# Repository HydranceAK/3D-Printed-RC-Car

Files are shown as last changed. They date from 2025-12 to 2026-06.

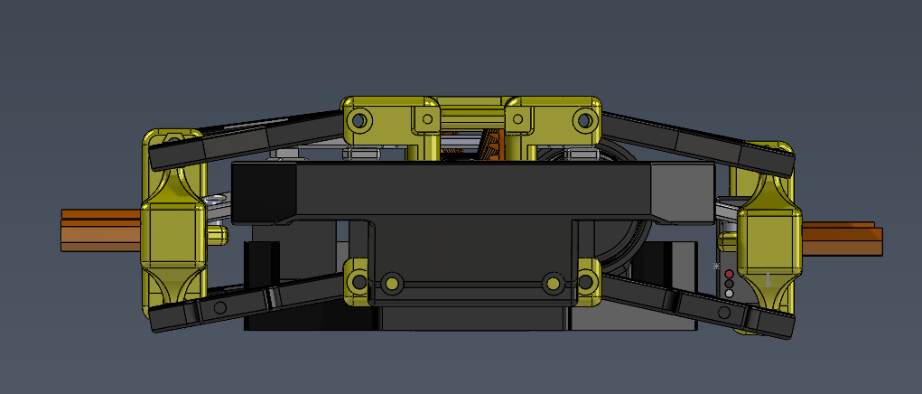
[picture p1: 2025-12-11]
Images & Videos/Screenshot 2025-12-07 164544.png

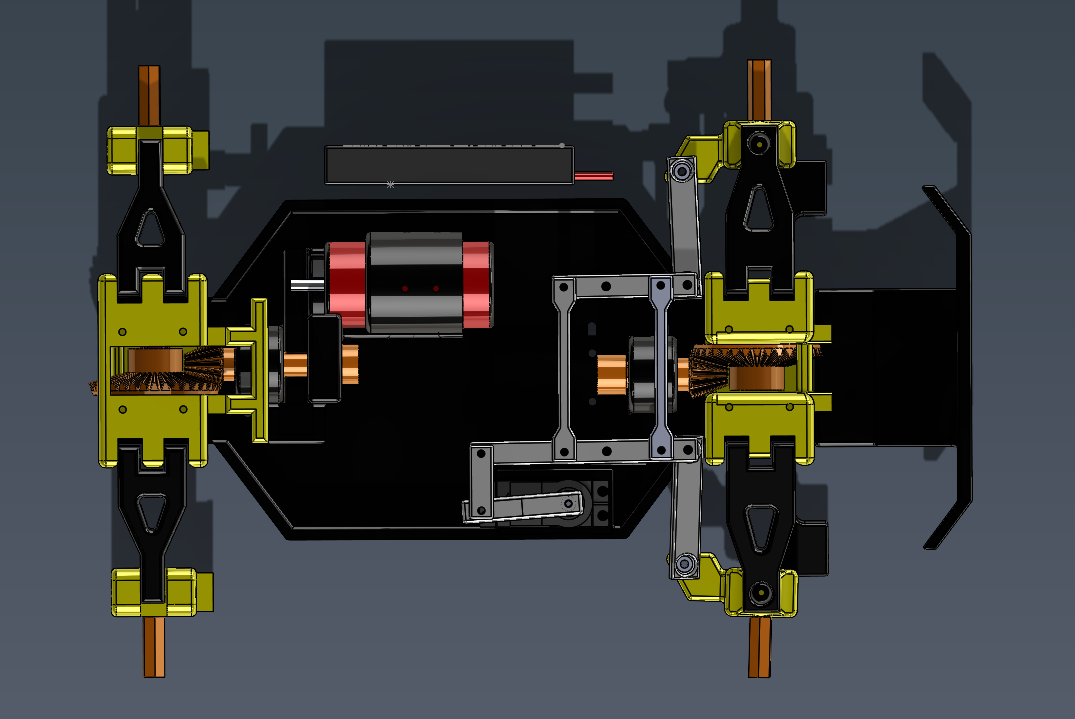
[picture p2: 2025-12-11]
Images & Videos/Screenshot 2025-12-07 164536.png

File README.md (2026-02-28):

**3D Printed RC Car**

A high-performance, fully custom 3D-printed RC car.

video: https://youtu.be/6iFeAaE8pu4

Designed and engineered by ***Hydrance***.

**Features**

* 4WD Drivetrain – Enhanced traction and stability.

* Top Speed: ~60 km/h – High-speed performance

* 90% 3D-Printed Build

* Independent Suspension 

* Durable Materials

* TPU parts for flexible components (tires, dampening mounts, impact zones)

* PETG parts for strong structural elements (chassis, arms, mounts)

* PA6-CF highly recommended but not nessecary for gears and bottom suspension arms. These peices undergo extreme stress and may break if you drive rough.  

* Affordable Build – Total estimated cost ~$330 (without screws \& filament $270)

**Materials \& Printing Notes**

TPU recommended for flexible and shock-absorption components

PETG recommended for strength, heat resistance, and rigidity

Everything can be printed on Bambu Lab a1 (0.4 or 0.6 nozzle)

Hardware, electronics, and drivetrain components sourced Amazon and AliExpress

**Disclaimer**

This project is provided for personal use only.

You may not sell, redistribute, upload, or copy this design without direct permission from the creator.

I am not responsible for any damage, injury, or misuse involving this design, its assembly, or its operation.

Operate RC vehicles safely and responsibly.

**Contact**

For permissions, questions, or collaboration, contact me at:

Email: abdusamaku@gmail.com

YouTube: https://youtube.com/@HydranceYT







WhatsApp Image 2026-01-09 at 2 21 19 PM

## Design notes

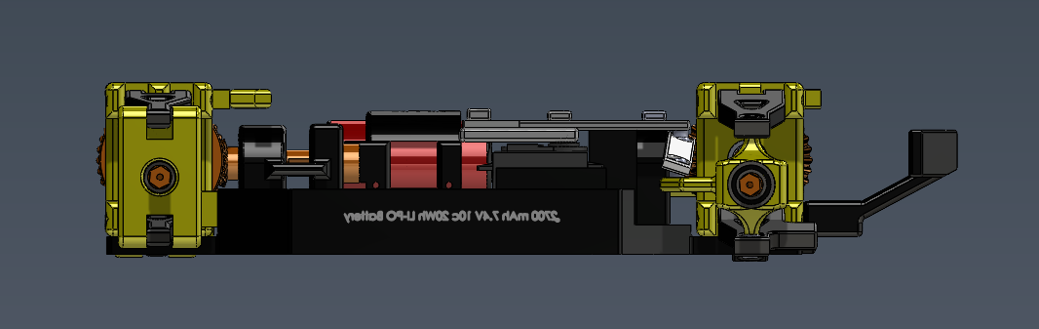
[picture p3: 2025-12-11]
Images & Videos/Screenshot 2025-12-07 164532.png

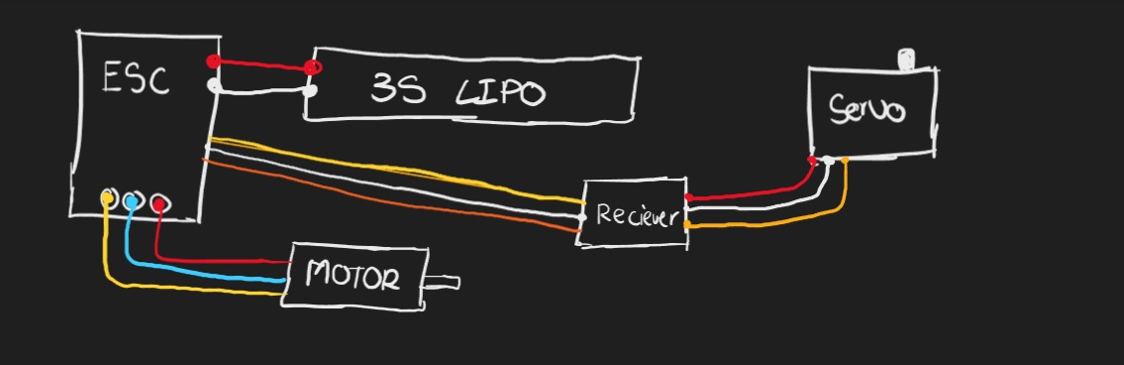
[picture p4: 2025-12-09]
Images & Videos/Circuit Diagram.png

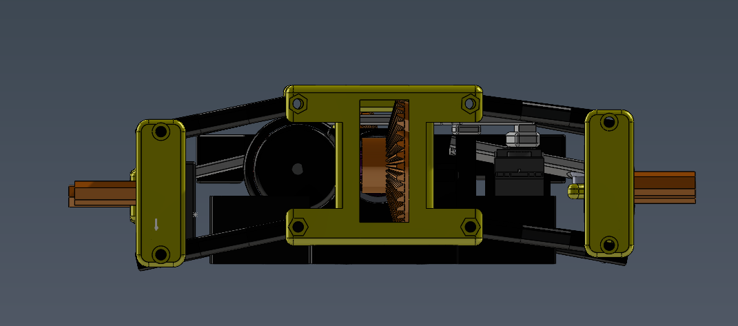
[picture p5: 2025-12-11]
Images & Videos/Screenshot 2025-12-07 164548.png

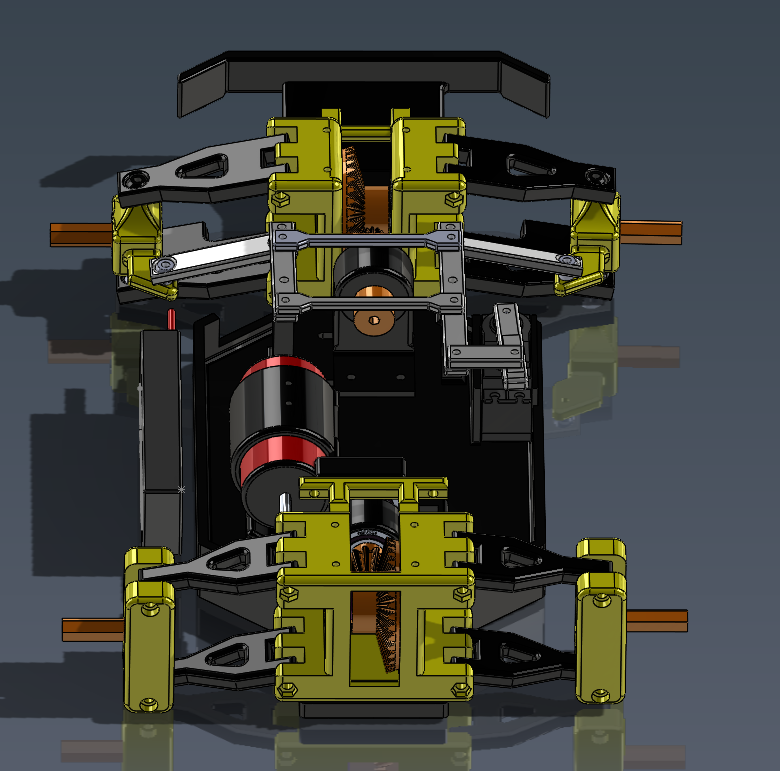
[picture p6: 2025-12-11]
Images & Videos/Screenshot 2025-12-07 164554.png

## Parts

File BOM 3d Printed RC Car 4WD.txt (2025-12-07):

NO DISCOUNTS Total Price: $334

Without Screws Total Price: $300

Without Filament Cost Total Price: $276

(You can get up to $50 off with discounts on AliExpress)

1x https://s.click.aliexpress.com/e/_c3Gsy9hf

1x https://www.aliexpress.com/item/1005010096604648.html

1x https://www.aliexpress.com/item/1005005858319911.html

1x https://www.aliexpress.com/item/1005006822635921.html

1x https://www.aliexpress.com/item/1005008314277777.html

1x https://www.aliexpress.com/item/1005007197683325.html

1x https://www.aliexpress.com/item/1005009497648073.html

1x https://s.click.aliexpress.com/e/_c3gM4Rg5

1x https://www.aliexpress.com/item/1005007572156636.html

4x https://www.aliexpress.com/item/1005006191847055.html

1x https://www.amazon.ca/gp/product/B09164YLNT/ref=ox_sc_act_title_3?smid=A3A5HQYFOGITKR&psc=1

1x https://www.amazon.ca/gp/product/B0BJQ87337/ref=ox_sc_act_title_6?smid=A11WJQJFCB3EYJ&psc=1

1x https://www.amazon.ca/gp/product/B08SJTPPPP/ref=ox_sc_act_title_7?smid=A3IVS9PE9W6NFK&psc=1

1x https://www.amazon.ca/gp/product/B08YD792LM/ref=ox_sc_act_title_8?smid=A249H9IR0LTI3Q&psc=1

1x https://www.amazon.ca/gp/product/B01DU4N8YM/ref=ox_sc_act_title_11?smid=A9BS2LDT3QKQL

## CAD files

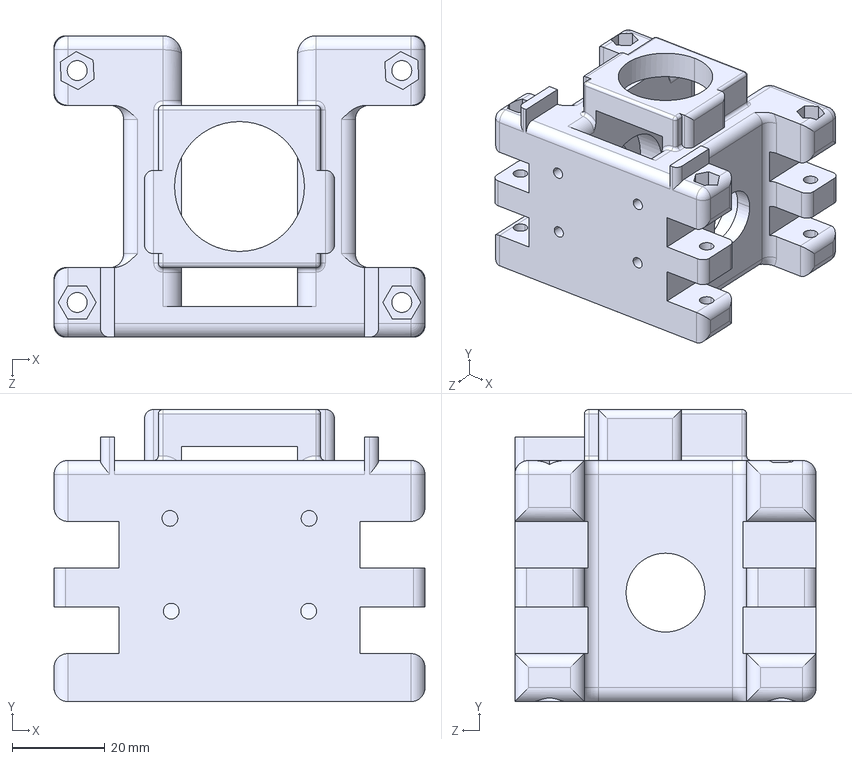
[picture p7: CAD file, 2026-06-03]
CAD Files/Main Suspension Hub Connector Front.STEP
80.0 x 63.0 x 65.0 mm

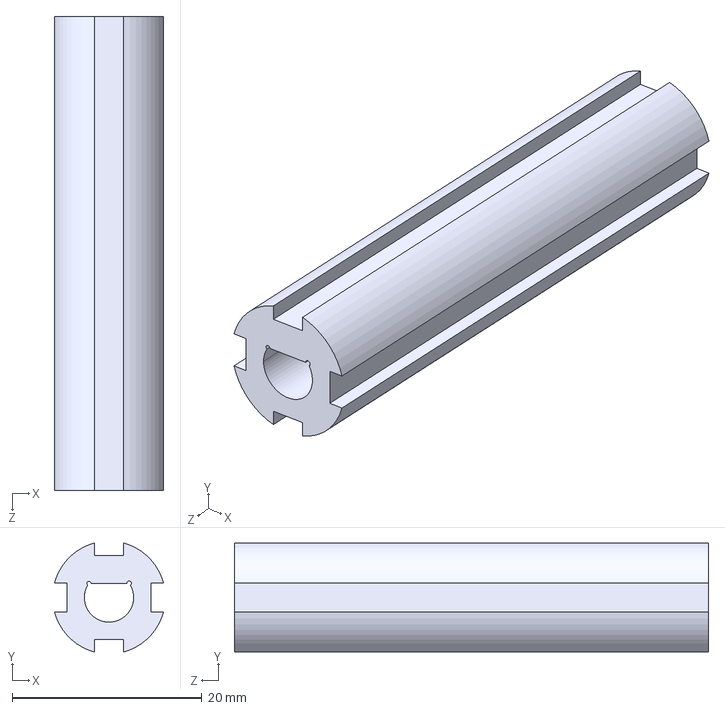
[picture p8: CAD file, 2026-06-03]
CAD Files/Main Rear Axle.STEP
11.5 x 11.5 x 50.0 mm

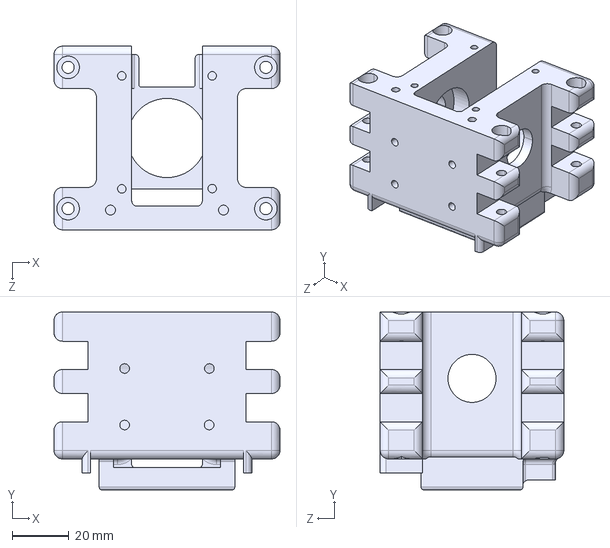
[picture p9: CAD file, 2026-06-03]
CAD Files/Main Suspension Hub Connector Rear.STEP
80.0 x 63.0 x 65.0 mm

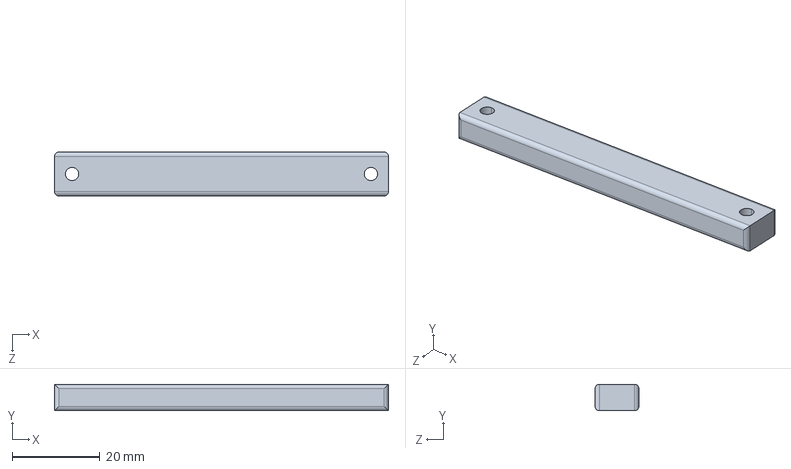
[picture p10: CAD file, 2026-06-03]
CAD Files/Main Connector Steering Arm.STEP
76.0 x 6.00 x 10.0 mm

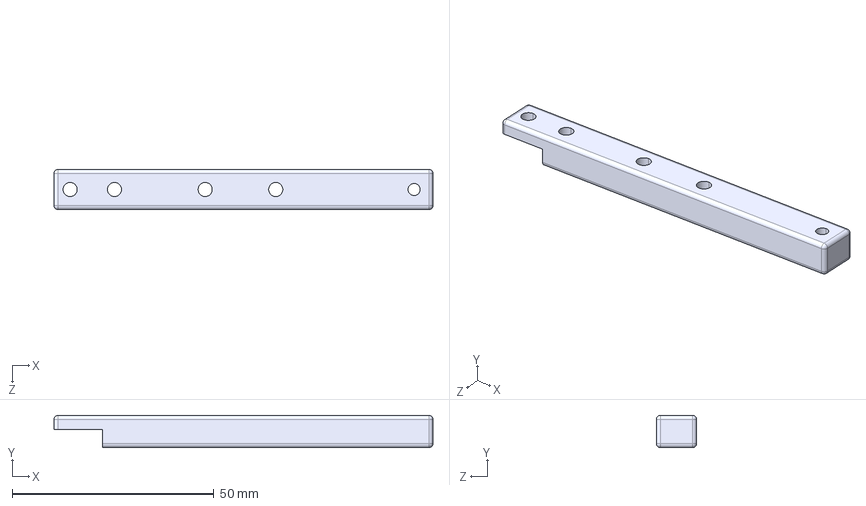
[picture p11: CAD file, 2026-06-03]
CAD Files/Steering Arm - Mini Right.STEP
94.0 x 8.00 x 10.0 mm

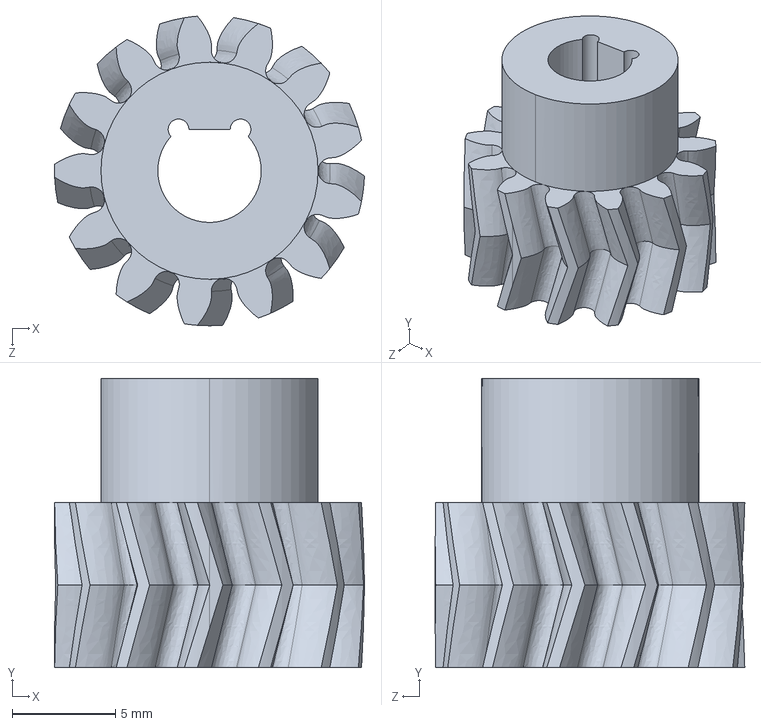
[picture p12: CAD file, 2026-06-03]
CAD Files/Spur gear (13 teeth).STEP
15.0 x 14.0 x 15.0 mm

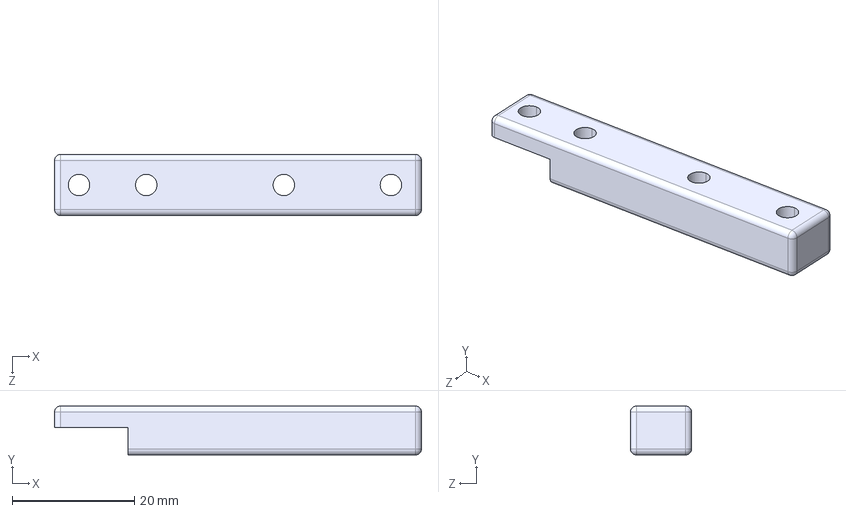
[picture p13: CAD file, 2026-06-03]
CAD Files/Steering Arm - Mini Left.STEP
60.0 x 8.00 x 10.0 mm

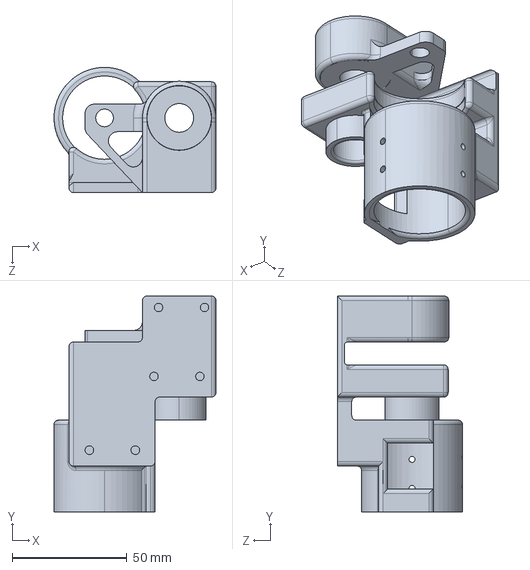
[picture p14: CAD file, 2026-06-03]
CAD Files/Motor Mount.STEP
70.5 x 94.0 x 54.5 mm

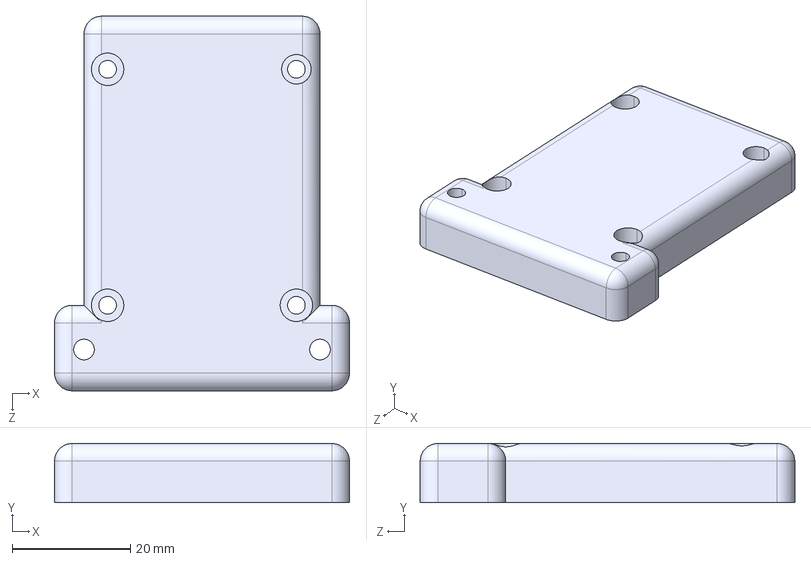
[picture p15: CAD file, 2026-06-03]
CAD Files/Rear Dust Cover.STEP
50.0 x 10.0 x 63.5 mm

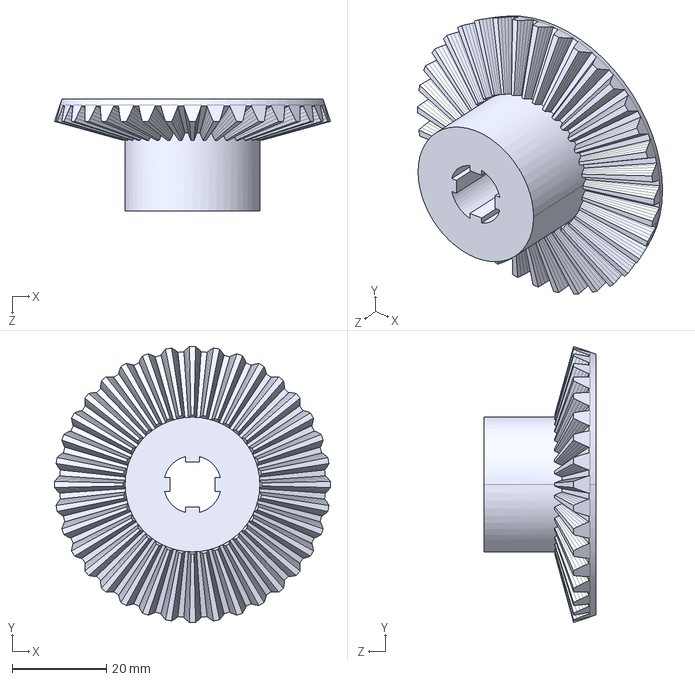
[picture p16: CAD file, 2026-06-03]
CAD Files/Large Bevel.STEP
58.5 x 58.5 x 23.7 mm

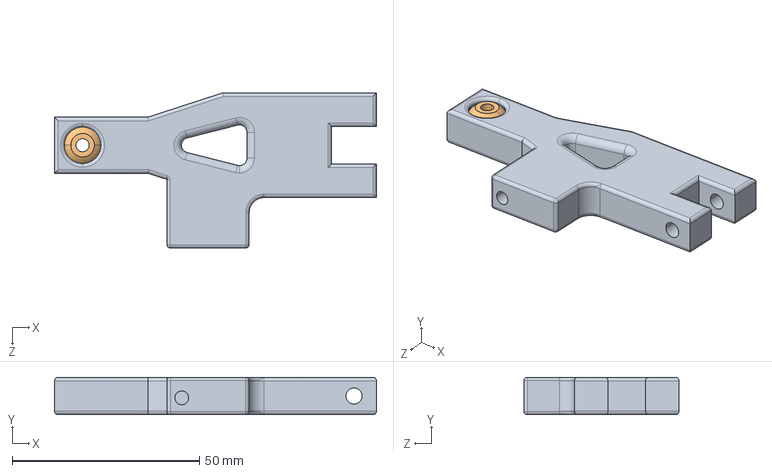
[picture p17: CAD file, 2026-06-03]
CAD Files/Front Suspension Arm bottom.STEP
86.0 x 10.0 x 41.5 mm
Front Suspension Arm bottom
Suspension Arm STEERING WHEEL BALL PIECE

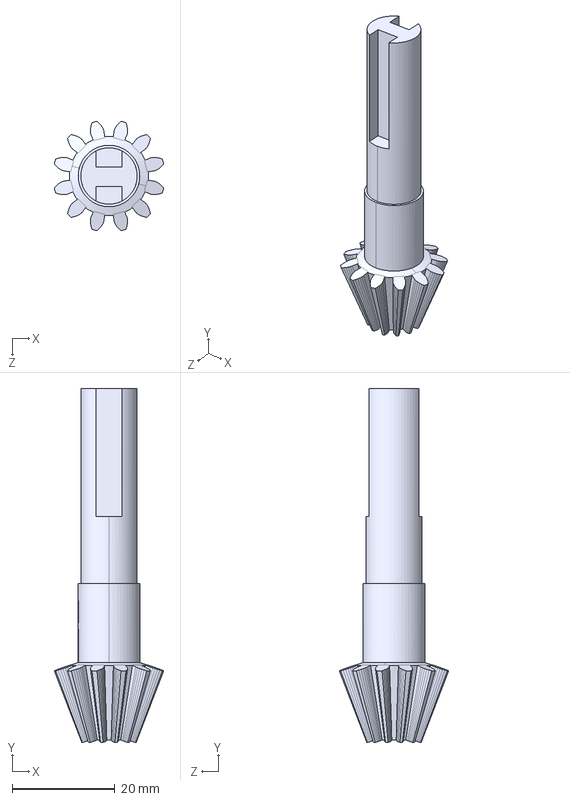
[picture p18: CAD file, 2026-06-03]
CAD Files/Larger Small Bevel.STEP
21.4 x 69.1 x 21.4 mm

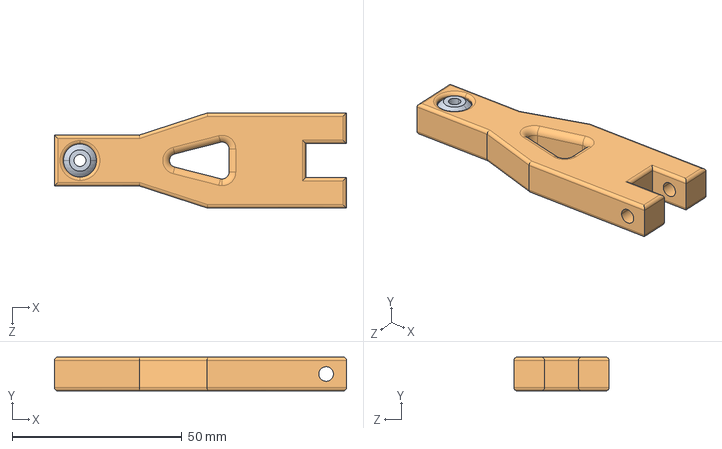
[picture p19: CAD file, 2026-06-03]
CAD Files/Front Suspension Arm top.STEP
86.0 x 10.0 x 28.0 mm
Suspension Arm STEERING WHEEL BALL PIECE
Front Suspension Arm top

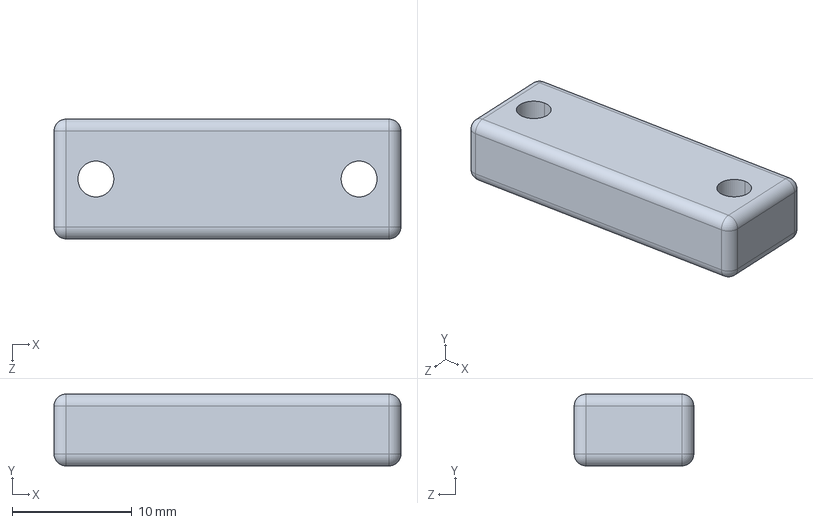
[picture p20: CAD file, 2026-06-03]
CAD Files/Servo To Steering.STEP
29.0 x 6.00 x 10.0 mm

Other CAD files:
CAD Files/Front Wheel Hub.STEP
CAD Files/Wheel Connector Rear.STEP
CAD Files/Rear Wheel Hub.STEP
CAD Files/Frame.STEP
CAD Files/Frame Cover.STEP
CAD Files/Front Dust Cover.STEP
CAD Files/Front Gear Mount.STEP
CAD Files/Front Shock Extension.STEP
CAD Files/Front-To-Rear Axle Connector.STEP
CAD Files/Rear Suspension Arm Bottom.STEP
CAD Files/Rear Suspension Arm Top.STEP
CAD Files/Servo Arm.STEP
CAD Files/Shock Absorber Extension - Rear Suspension Hub.STEP
CAD Files/Smaller Bevel.STEP
CAD Files/Spaced.STEP
CAD Files/Spoiler.STEP
CAD Files/Steering Arm.STEP
CAD Files/Upgraded Bumper.STEP
CAD Files/Wheel Connector Front.STEP
CAD Files/Wheel Spacer Rear.STEP



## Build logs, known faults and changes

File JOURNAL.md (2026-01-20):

<!--
  This journal is auto generated by Hack Club Blueprint.
-->

## 12/3/2025 - I've completed prototype #1 for my steering and suspension  

_Time spent: 3.0h_  




Changed the suspension mount from the wheel hub to the suspension arm. I don't know how I was silly enough to mount the shocks to the wheel hub, it just forcefully turned it making the steering useless xD. Fixed that now and am 3d printing a prototype right now to see how it works.   

## 12/4/2025 6:30 AM - 3d printed prototype  

_Time spent: 2.0h_  

I 3d printed my suspension prototype with normal PETG filament. Hoping to get some PETG-CF but out of range right now.

The suspension assembly works pretty flawlessly, one of the steering is a little rough but im sure it'll grind itself in soon.

WhatsApp Image 2025-12-04 at 9.25.57 AM (1)WhatsApp Image 2025-12-04 at 9.25.57 AM (2)
WhatsApp Image 2025-12-04 at 9.25.57 AM

## 12/4/2025 6:38 AM - Suspension Arm Adjustment  

_Time spent: 0.2h_  

Made a minor adjustment to the suspension arm assembly so that it prints better. The suspension arm had a tiny overhang that caused ugly supports, so I removed it in all. Also added a little more clearance to the suspension hub so the arms have more movement.





## 12/4/2025 8 AM - Printed Steering System  

_Time spent: 2.0h_  

I 3d printed the steering prototype #1.

Put it all together and noticed some of the clearances are too tight, for now i just drilled through them, but ill update the CAD for the final design.

Once the frame is printed tomorrow i can put everything together and test it.

WhatsApp Image 2025-12-04 at 11.24.00 AM

## 12/5/2025 - Redesigned the steering mechanism  

_Time spent: 4.0h_  

So I realized that my steering mechanism is only giving me a few degrees of rotation/steering which is too less for my use. I changed the geometry, lengths etc to allow for greater steering angle along with stronger and more efficient use. 

Heres what it looks like now:




## 12/10/2025 9 AM - Edited The Suspension Hub  

_Time spent: 5.0h_  

After some testing with the drive train, I noticed the gears were cracking due to skipping. This made it pretty much unusable. 

So I added this "support" for the bevel gear so that is it always directly perpendicular and meshed with the larger bevel gear. This way it's pretty much impossible for it to skip gears, unless it breaks of course. I did this for both the front and rear suspension hub.

Ill try printing some prototypes to see how it works.



## 12/10/2025 8 PM - Edited The Wheel Hubs  

_Time spent: 2.0h_  

I changed the hole diameters on the rear wheels hubs to be smaller, therefore a smaller tolerance and less shake. Because during my testing the tires were vibrating too much.

I also changed the hole diameter on the front wheel hub so that the universal joint's screws wouldn't rub against the wall.

(I also made everything black in the design and it looks MUCH better, can wait to show you the 3d printed parts once complete.)




## 1/1/2026 10:29 AM - Completed the drive train  

_Time spent: 5.0h_  

I completed the entire drive train. I realized that the small gears were not correctly meshed with the large bevel gears which caused gear skipping and wear, its now all fixed and works pretty flawlessly.

The front gearbox is connected to the rear gearbox using a small 4mm circular shaft with a cut indent, like in brushless motors shafts. 

I also polished all the wheel hubs, suspension hubs, and frame. Added chamfers, fillets, removed extra material etc. 



## 1/1/2026 10:31 AM - Redesigned the bumper  

_Time spent: 1.0h_  

Since my last bumper out of TPU was too flimsy and weak, I made some adjustments to the design to make it stiffer. The main one being adding those tiny supports on the middle of the bumper, they look like small additions but they completely change the behavior of the bumper. 

Now its much stronger and stiffer and will actually absorb high speed crashes or bumps. 



## 1/1/2026 10:34 AM - Added texts / water marks  

_Time spent: 0.1h_  

Never did this before but seems kinda nice so I added my own text & watermark. 

Put my channel on the bottom and the specs of the car on the side. Let me know how it looks :)



## 1/4/2026 5:36 PM - Built a Spoiler  

_Time spent: 1.0h_  

I made a spoiler.

Went online and found some inspiration and then created my own from there. 






I tried to make it as aerodynamic as possible so it serves as much purpose as possible and gives me downforce rather than just being for show. 

## 1/4/2026 5:38 PM - Created a dust/snow/debris cover  

_Time spent: 3.0h_  

I finally decided to make a cover for the car. Snow and Dirt and become pretty annoying to clean after a while. I also made the design as waterproof as possible.









## 1/4/2026 5:40 PM - Latest Version  

_Time spent: 1.0h_  

This is the latest complete version of the car.

Upgrades from previous version:

- spoiler
- cover
- waterproofing
- 4WD completed
- thicker arms / stronger
- polished steering assembly
- watermarks

Everything is polished in this design.




## 1/7/2026 9:35 AM - Prepared the 3mf and printed all the parks  

_Time spent: 2.0h_  

I've put all the car parts and files in my slicer and prepared them all. 

The total comes to about 1kg of filament, which is around $33. Not too bad of a price at all. 



## 1/7/2026 9:44 AM - Printed and put together all the parts  

_Time spent: 12.0h_  

I've printed everything and put together the car!

WhatsApp Image 2026-01-07 at 12.38.27 PM (1)
WhatsApp Image 2026-01-07 at 12.38.27 PM

It looks amazing honestly. 

I recorded the entire build and am going to make a video of it soon. Here's some images of the build process: 




I've spent a TON of time troubleshooting and putting this thing together. Although the actual build parts are only 1kg in filament, ive spent more than 3kg just with the prototyping and old parts. Im going to upload images of them soon. 

## 1/7/2026 9:52 AM - Test Parts Showcase   

_Time spent: 1.0h_  

WhatsApp Image 2026-01-07 at 12.47.54 PM (2)
WhatsApp Image 2026-01-07 at 12.50.35 PMWhatsApp Image 2026-01-07 at 12.47.54 PM (3)WhatsApp Image 2026-01-07 at 12.47.54 PM (1)
WhatsApp Image 2026-01-07 at 12.50.25 PMWhatsApp Image 2026-01-07 at 12.47.54 PM

These are all the parts I've printed for testing or previous versions while creating this projects. Some parts were either too weak and broke, other had minor clearance or fitting issues, and other were, well, just older version and weren't the most effective way to do it and i upgraded.

All the stuff in the images are probably 2kg of filament.

## 1/9/2026 - Test Drove the Car  

_Time spent: 4.0h_  

Here are some videos and clips from the test drives! It works amazing honestly, goes extremely fast, has superb control with the 4WD, and hasn't been facing much issues. Only thing I noticed while driving it really fast and turning is one of the front wheels lifts off the ground which leads the car to turn one way. I may need to soften the suspension to fix this. 

[Car Video](/user-attachments/blobs/proxy/eyJfcmFpbHMiOnsiZGF0YSI6NzkwNzIsInB1ciI6ImJsb2JfaWQifX0=--98f6d8ae577e43a6995309cbd1f4d47fd830c12c/Car%20Video.mp4)



I tested the car in many other places, ill upload those videos soon too!  

## 1/12/2026 2 PM - Updated the frame  

_Time spent: 8.5h_  

After a lot of testing, nearly everything seemed perfect..

but then I was driving the car in an icy parking lot at near max speeds, and all of a sudden it lost control and barrel rolled at terminal velocity...

however NOTHING but the frame broke, which is honestly amazing, even though everything was put through extreme stress, it stood together. The TPU parts definitely contributed to this success. 

And I actually fore-saw the failure in the frame, its the one week spot that broke in all my previous prototypes. 

So after tens of hours of testing, driving, stress testing, i've perfected the design (for now).

For now, I've added these modifiers in the slicer settings to strengthen the parts of failure.




I also increased the infill by 5%.

I'm currently printing this, and we'll see how it stands after testing.

## 1/12/2026 3 PM - Purchased and fitted the new tires  

_Time spent: 2.0h_  

From the money I got from the grant, I purchased new bearings and tires for the wheel assembly. The new tires work wonderfully, only down side it that my steering angle is reduced a little because of the larger width from these tires.

These tires have much better grip and stand perfectly. 

Here what they look like: 

WhatsApp Image 2026-01-09 at 2.21.19 PM

## 1/12/2026 6 PM - Redesigned the Frame Cover  

_Time spent: 4.0h_  

After my latest high speed crash, I noticed that I'll need a little more support for the suspension hubs so that the frame doesn't snap like last time. 
Thus I added these extensions on the frame cover which screw onto the suspension hubs.



Ill print this soon and update on how effective it is.

It should at the least remove a reasonable amount of tensions from the frame. 

## 1/13/2026 7 AM - Printed the new prototype  

_Time spent: 4.0h_  

I printed the new version of the frame cover, and it works pretty good. It's stiff and strong, and will definitely add some rigidity to the overall model. 

WhatsApp Image 2026-01-13 at 10.48.29 AM

## 1/13/2026 1:36 PM - Made some changes to wheel spacer + fitter  

_Time spent: 2.0h_  

I made some clearance edits to the wheel spacer and fitter. They were too tight, especially on the PA6-CF parts, so I increased the inner diameter. I also had to adjust the length a bit so it fit correctly.

printed them in PETG, and tested. They work good.





## 1/13/2026 1:55 PM - Made some changes to the Front Top Suspension Arm  

_Time spent: 2.0h_  

The top front suspension arm was wiggling too much, which is something Im guessing contributed to my recent barrel role crash. the wiggle / vibration can cause distortions in the wheel which will send the car off track. I fixed this by making the ball piece a bit larger, hence tighter.

Ill print it with TPU later today and update on how it goes. 



## 1/13/2026 2 PM - Final Result!  

_Time spent: 2.0h_  

With the new wheel spacers, wheel fitters, wheel connectors, upgraded frame, upgraded frame cover, everything looks AWESOME!

It drives like a beast, really sturdy and strong, and was a blast to make.

WhatsApp Image 2026-01-13 at 5.05.25 PM
WhatsApp Image 2026-01-13 at 5.05.24 PM

I don't think Im going to make any major changes now. It's safe to say this project is now wraps!  

## 1/17/2026 - Finishing Touches  

_Time spent: 10.0h_  

After driving the car for a LONG time, I found some minor issues or stuff that could be improved. I wont go in detail for each of the changes but here is an overview:

- Aesthetic changes
- Extra Material removal
- Suspension Adjustment (harder)
- Front Sus Hub thickened (stronger)
- Frame Cover Adjustments (visual and functional)
- Wheel Spacer Adjustment (stronger)
- Front To Rear axle connecter adjustment (stronger)
- Rear Suspension Extension adjustment (redesign)
- Finishing touches






WhatsApp Image 2026-01-09 at 2.21.19 PM

## 1/19/2026 - Final Look  

_Time spent: 5.0h_  

Here's a final look at the RC Car project.

Everything has been touched, some more changed to the motor mounts and steering assembly (it broke while testing so i reinforced it)

And here's what it looks like. 



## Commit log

2025-12-07 Create Full CAD Assembly (including electronic componenets).md
2025-12-07 Rename BOM.csv to BOM (for grant).csv
    [BOM (for grant).csv]
2025-12-11 Create cad
2025-12-11 Create STL
2026-03-19 Delete CAD Files/STEP Files.zip
    Incorrect file
2026-03-19 Delete CAD Files/Cad
    n/a
